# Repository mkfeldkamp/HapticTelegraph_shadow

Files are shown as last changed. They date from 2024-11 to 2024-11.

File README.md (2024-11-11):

# HapticTelegraph

The Haptic Telegraph is an open-source educational project to learn the basics of mechatronic sensing and control of motion, force, and impedance for one or more degrees or freedom along with basi teleoperation.  Inspired by the [HapKit](https://hapkit.stanford.edu/) open source Haptics learning project, the the haptic telegraph has two degrees of freedom (DOF) with the option to teleoperate over the internet and interconnect different haptic telegraphs to experiment with bilateral teleoperation.  

The platform uses a Teensy 4.0 microcontroller and breadboard to allow prototyping and easier modifications.  Sensing includes potentiometers, encoders, and load cells (HX711); actuators include hobby servos, N20 gearmotors, and direct-drive DC motors; an DRV8833 H-Bridge for driving up to two DC motors, and a simple way of attaching actuators in various configurations.  This includes side-by-side configurations or serlial linkages like a 2-link revolute joint robot with integrated torque sensing. 

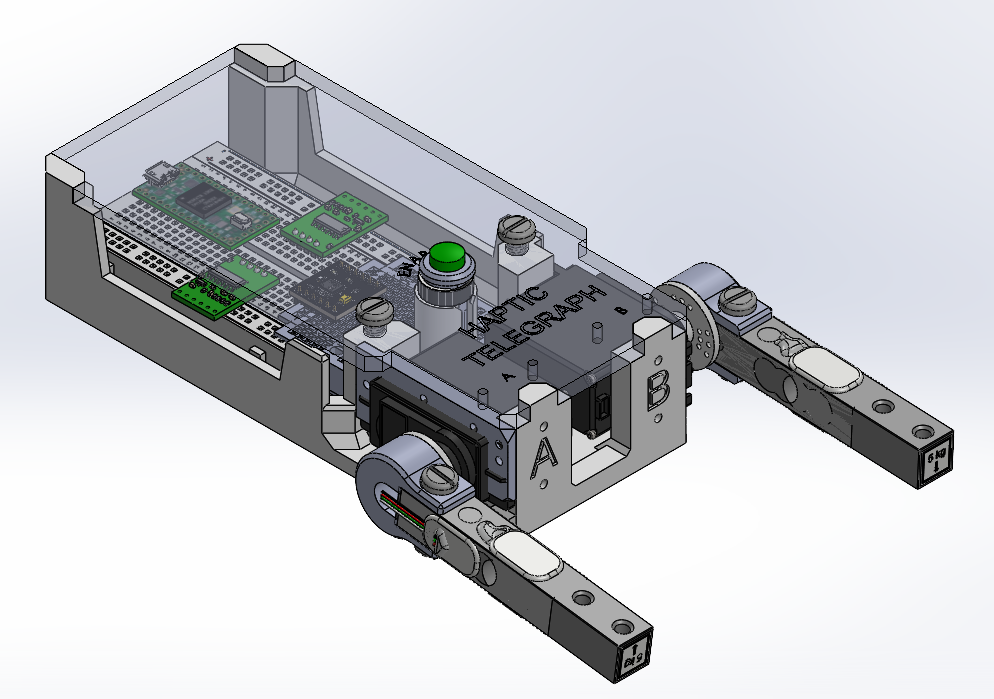
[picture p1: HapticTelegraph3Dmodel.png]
The Haptic Telegraph


## Building and Assembly 
All parts required for the different configurations of the telegrpaph are linked here.  The kit has hobby servo motors, N20 gear motor+encoders, direct drive DC motor for capstan, or DC motorized slide-potentiometer actuators.  The servo and N20 configurations are the default.  

[Haptic Telegraph Assembly Guide](https://docs.google.com/document/d/17Dt6qZLQLV2zLom0jG1yqs2Jcs7Xk3iRWMrtn3mGbbk/preview)

[BOM and Kit Inventory](https://docs.google.com/spreadsheets/d/1TIM3guZMqlwLRaXGF0uH3Ged3IqBKqTgrUTtAIh1ZG8/preview)

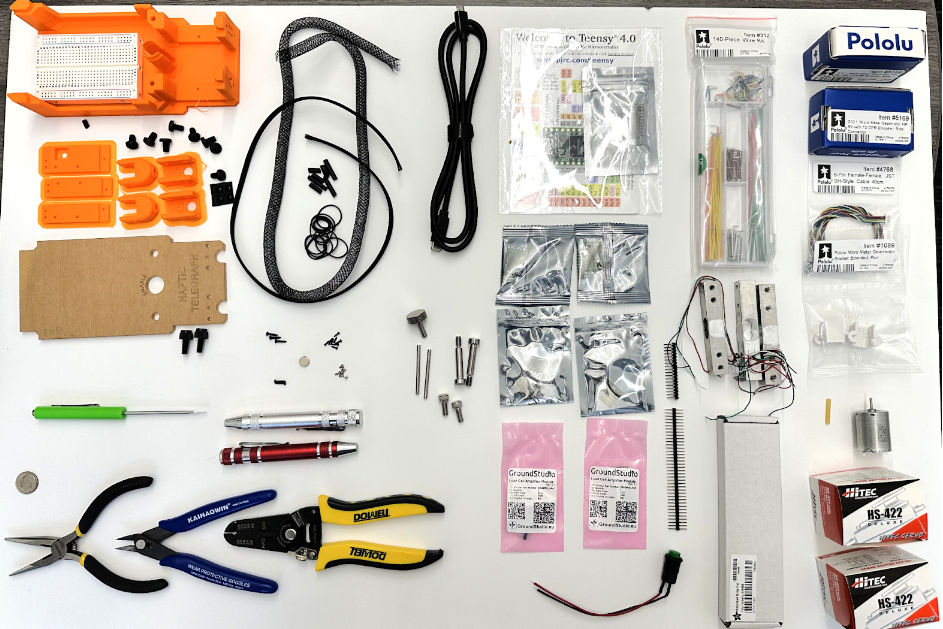
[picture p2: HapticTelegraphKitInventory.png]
Parts Kit Inventory


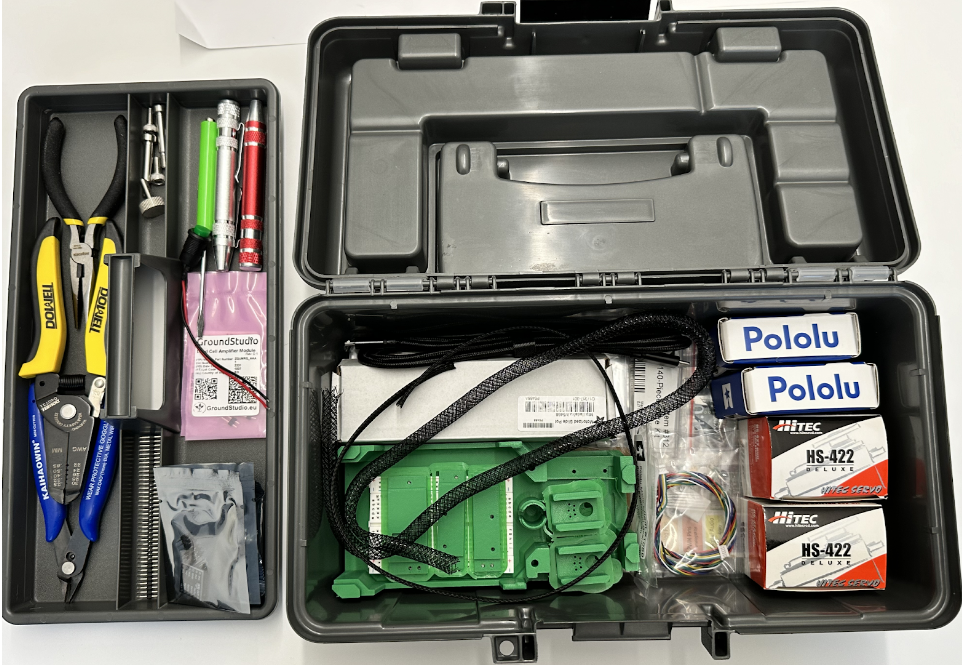
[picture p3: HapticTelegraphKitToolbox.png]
Kit Toolbox


## Software and Firmware
A brief introduction to the python scripts to teleoperate the kit and to run the firmware can be found here: <br>
[Haptic Telegraph Software Guide](https://docs.google.com/document/d/1zL3_G8BJS4lk9wN5zXE0Af6u3FeUNIUszWQ2UWdJn5c/preview)

## Resources
A great intro to haptics, teleoperation, and related terminology can be found here:
[Do It Yourself Haptics: Part I](https://ieeexplore.ieee.org/document/4437756)    
V. Hayward and K. E. Maclean, "Do it yourself haptics: part I," in IEEE Robotics & Automation Magazine, vol. 14, no. 4, pp. 88-104, Dec. 2007, doi: 10.1109/M-RA.2007.90792

A widely acclaimed, more thorough treatment from Prof. Allison Okamura is here:
https://web.stanford.edu/class/me327/

### Info
ME8284 Intermediate Robotics with Medical Applications Graduate Level Course <br>
University of Minnesota Mechanical Engineering, Fall 2024 <br>
Prof. Timothy M. Kowalewski, timk@umn.edu
Pin-Hao Cheng, cheng741@umn.edu

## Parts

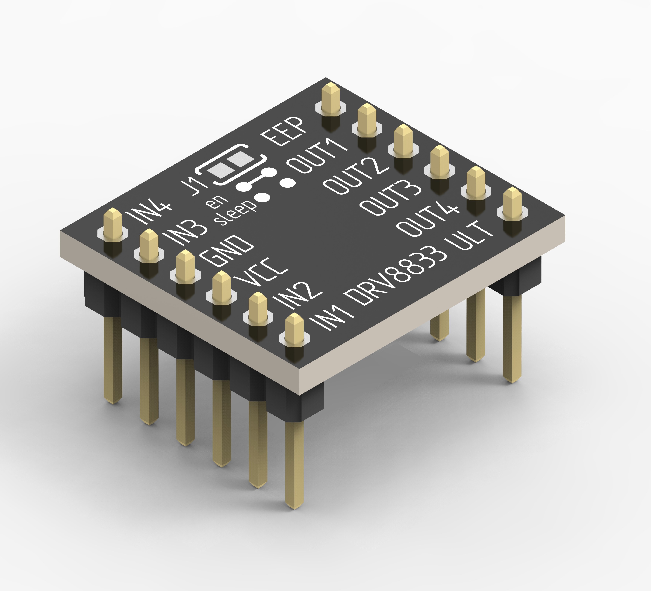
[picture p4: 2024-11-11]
mechanical/stockParts/etc/drv8833-doble-puente-h-dual-h-bridge-motor-driver-1.snapshot.3/Modulo DRV8833/Renders/Modulo_DRV8833_B.24.jpg

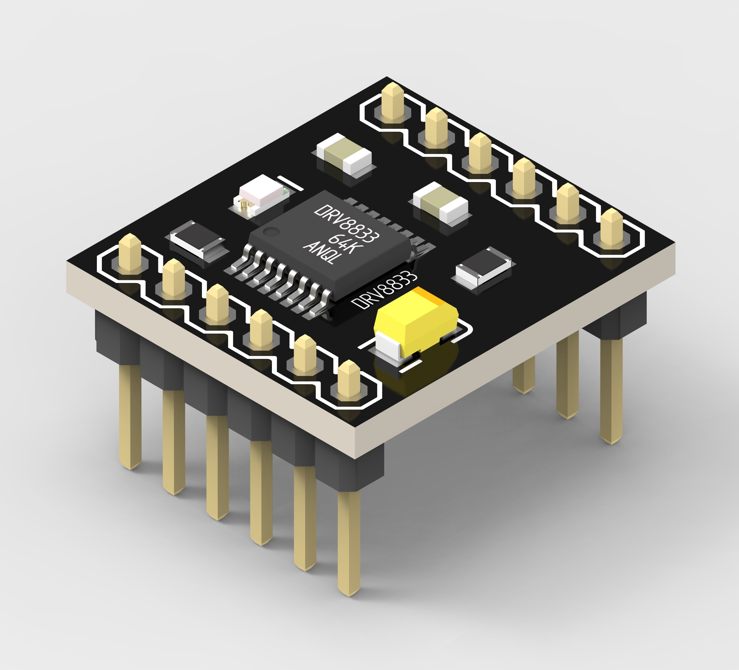
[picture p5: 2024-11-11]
mechanical/stockParts/etc/drv8833-doble-puente-h-dual-h-bridge-motor-driver-1.snapshot.3/Modulo DRV8833/Renders/Modulo_DRV8833_A.jpg

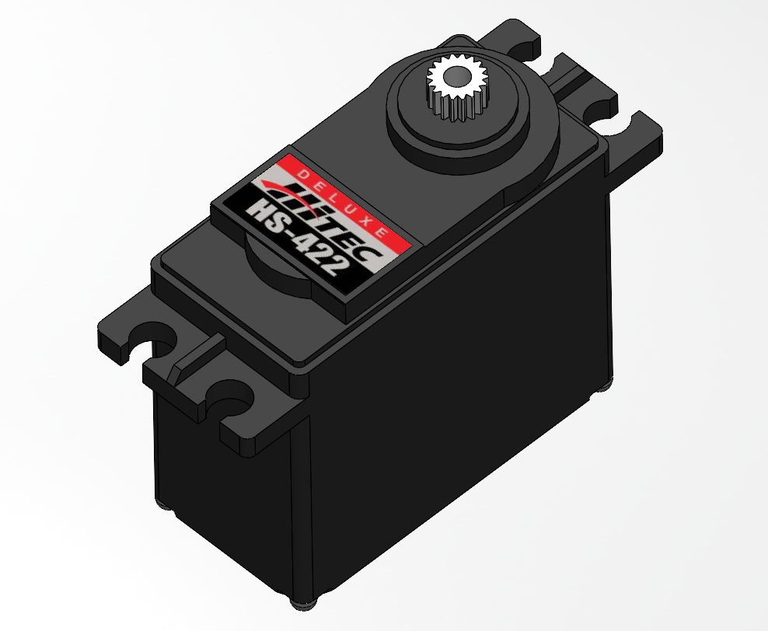
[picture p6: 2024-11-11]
mechanical/stockParts/etc/hitech-servo-hs-422-1.snapshot.10/Renders/Hitec-422 ServoMotor 1.png

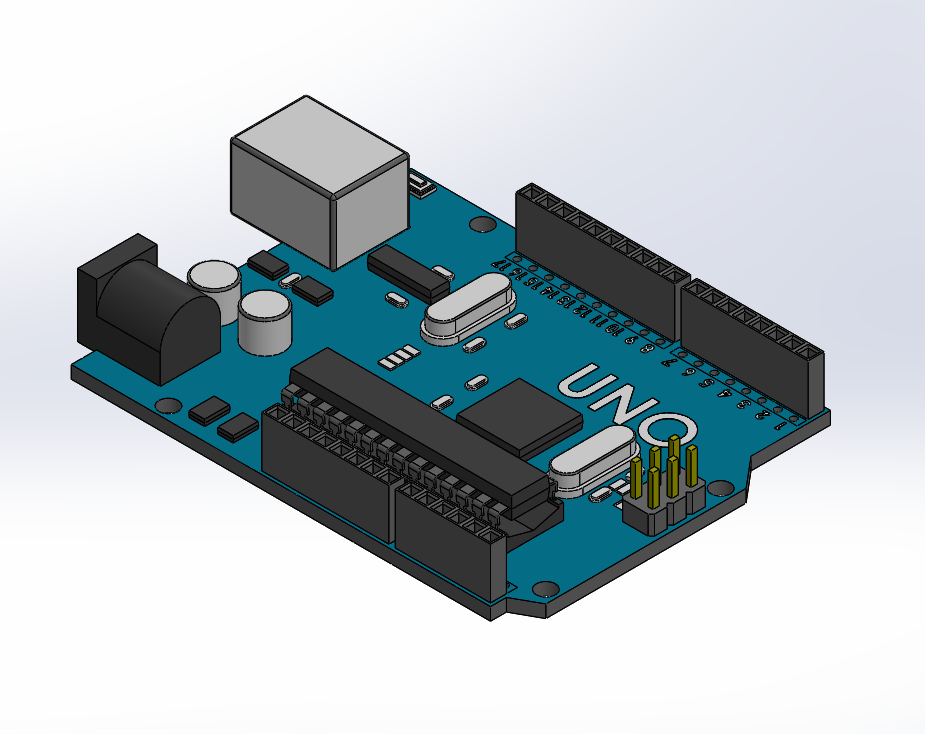
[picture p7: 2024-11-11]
mechanical/stockParts/etc/arduino-uno-62.snapshot.2/Arduino UNO.png

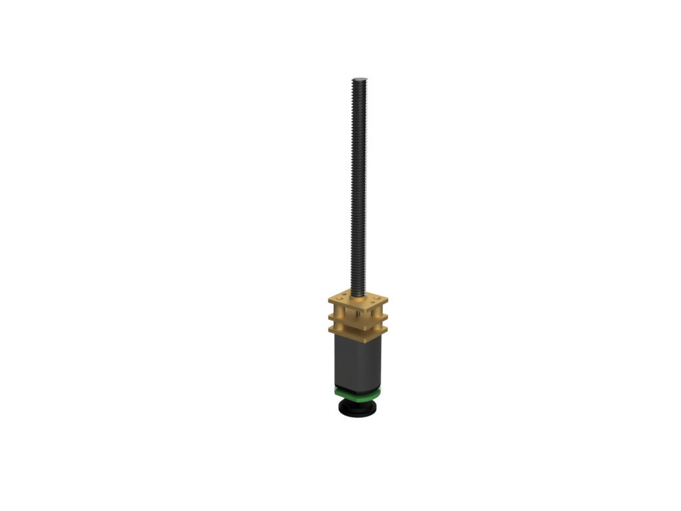
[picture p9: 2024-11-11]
mechanical/stockParts/etc/n20-gearbox-encoder-m4x55mm-1.snapshot.3/n20 encoder m4x55.png

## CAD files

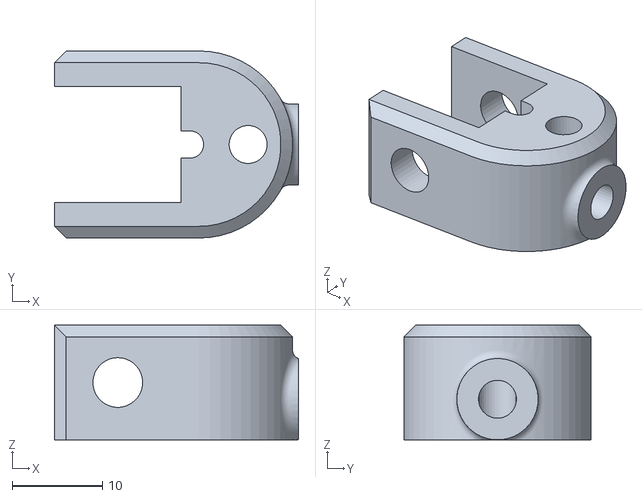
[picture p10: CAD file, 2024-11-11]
mechanical/3D printing and gCode/D Shaft Coupling N20.STL
27.0 x 20.7 x 12.7

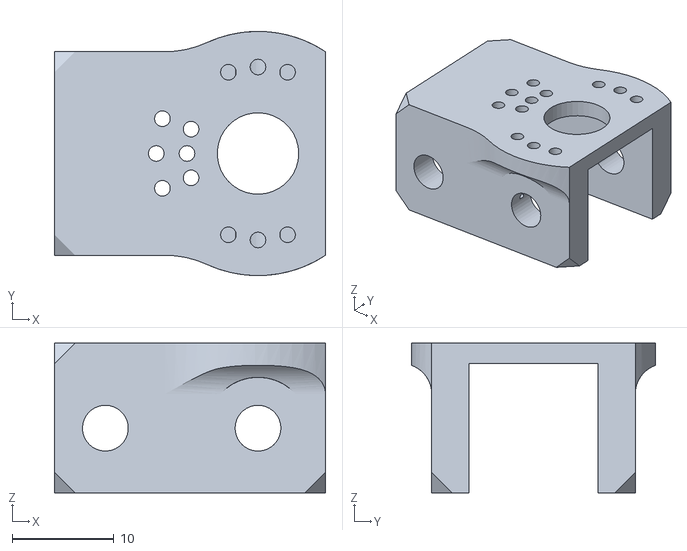
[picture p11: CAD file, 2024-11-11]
mechanical/3D printing and gCode/TOpRINT/1kg 80mm Load Cell Servo Horn Mount.STL
26.6 x 24.0 x 14.7

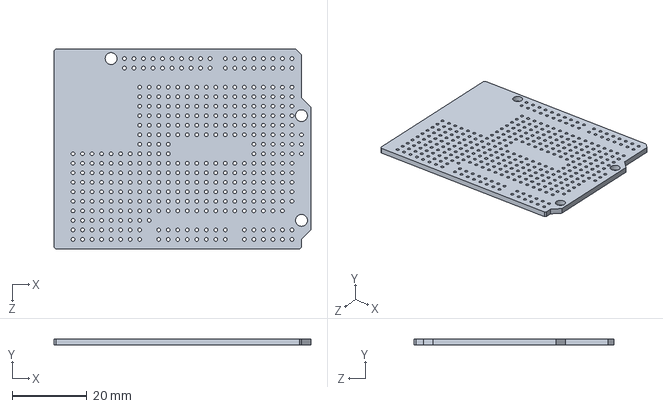
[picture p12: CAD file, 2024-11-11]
mechanical/stockParts/etc/arduino-proto-shield-r3.snapshot.3/Arduino proto shield R3.SLDPRT
68.6 x 1.70 x 53.3 mm

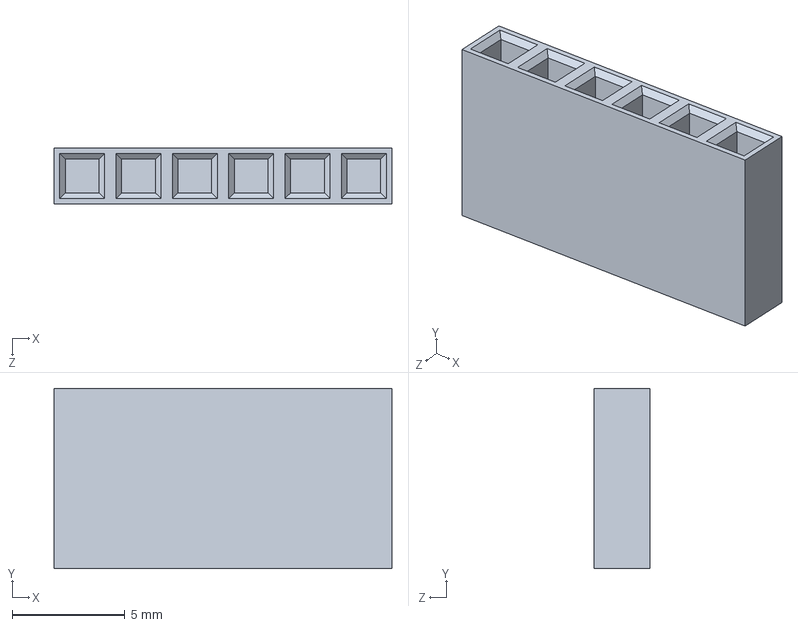
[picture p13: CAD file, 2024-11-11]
mechanical/stockParts/etc/arduino-uno-62.snapshot.2/Pins Socket 4.SLDPRT
15.0 x 8.00 x 2.50 mm

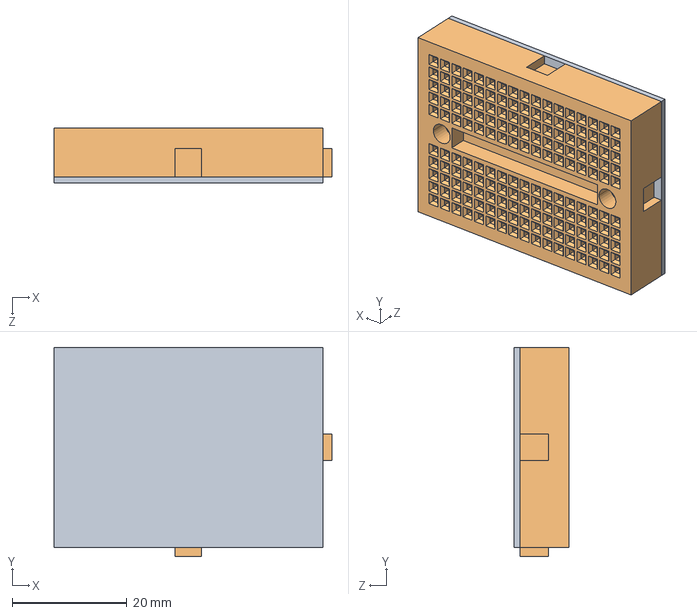
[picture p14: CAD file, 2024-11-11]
mechanical/stockParts/etc/breadboard-22.snapshot.4/BreadBord.STEP
48.4 x 36.4 x 9.50 mm

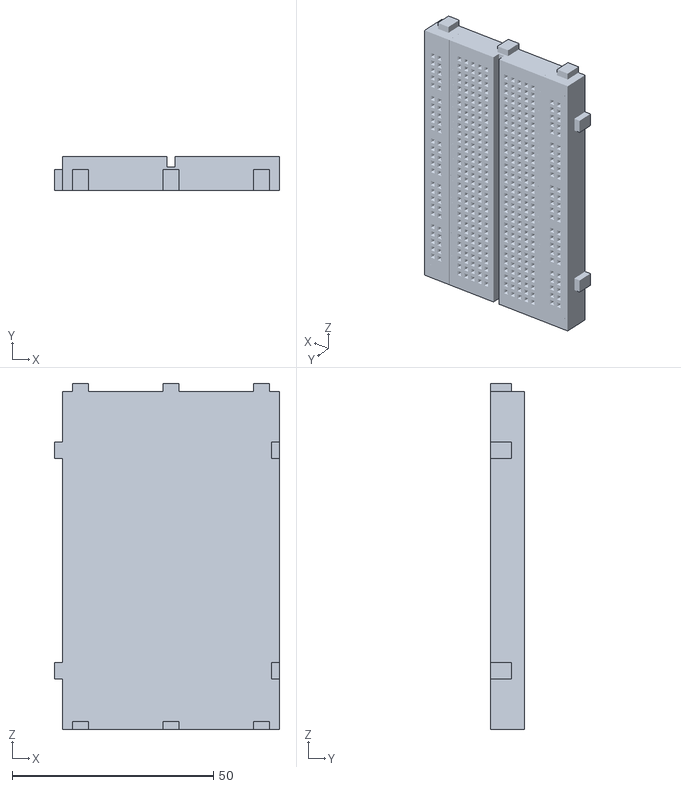
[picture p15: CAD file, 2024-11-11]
mechanical/stockParts/etc/breadboard-400-1.snapshot.5/Breadboard 400.stl
56.0 x 8.41 x 86.0

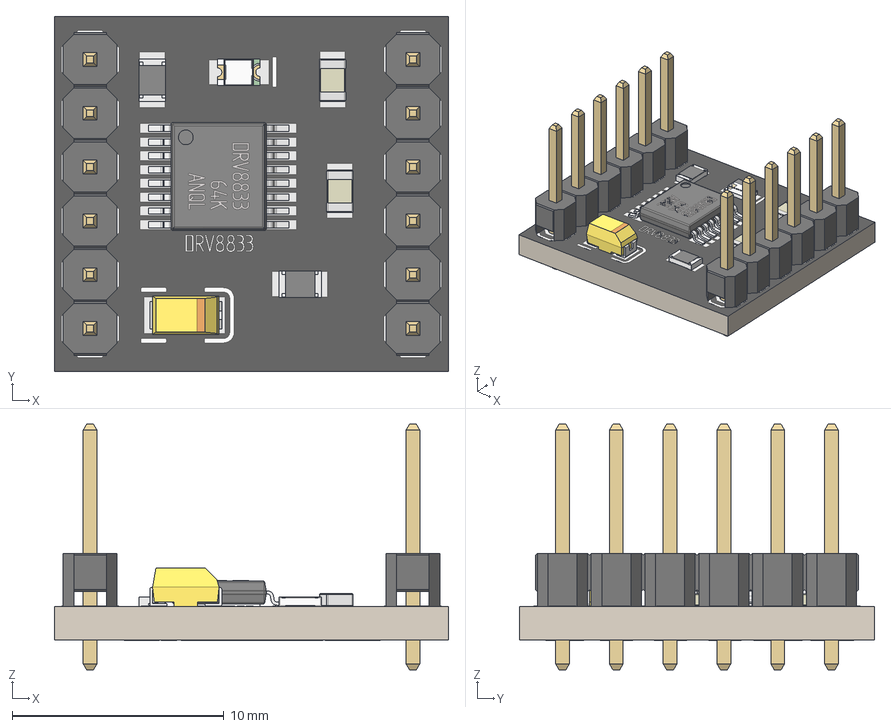
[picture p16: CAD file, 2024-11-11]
mechanical/stockParts/etc/drv8833-doble-puente-h-dual-h-bridge-motor-driver-1.snapshot.3/Modulo DRV8833/Modulo_DRV8833_B.stp
18.6 x 16.8 x 11.6 mm
placa
TSSOP_cuerpo_1.2h
TSSOP_pin_6.6 x 2
PIN_macho_1x6 x 2
T494A
C0805_060 x 2
R0805 x 2
housing
marking x 2
cover
base_2
base

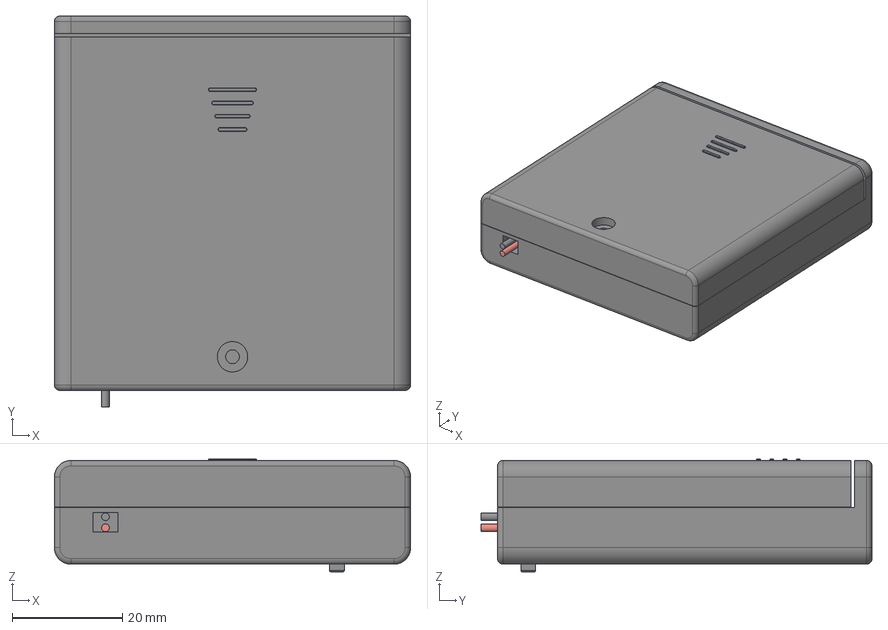
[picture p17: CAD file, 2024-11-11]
mechanical/stockParts/etc/enclosed-4-aa-battery-holder-1.snapshot.25/batteryHoder.step
64.5 x 70.8 x 20.4 mm

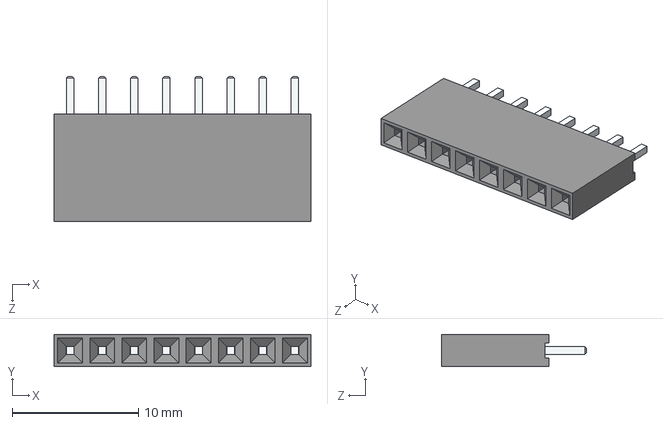
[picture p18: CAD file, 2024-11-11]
mechanical/stockParts/etc/female-header-2-54-1xn-1.snapshot.3/FemaleHeader.STEP
20.3 x 2.54 x 11.5 mm

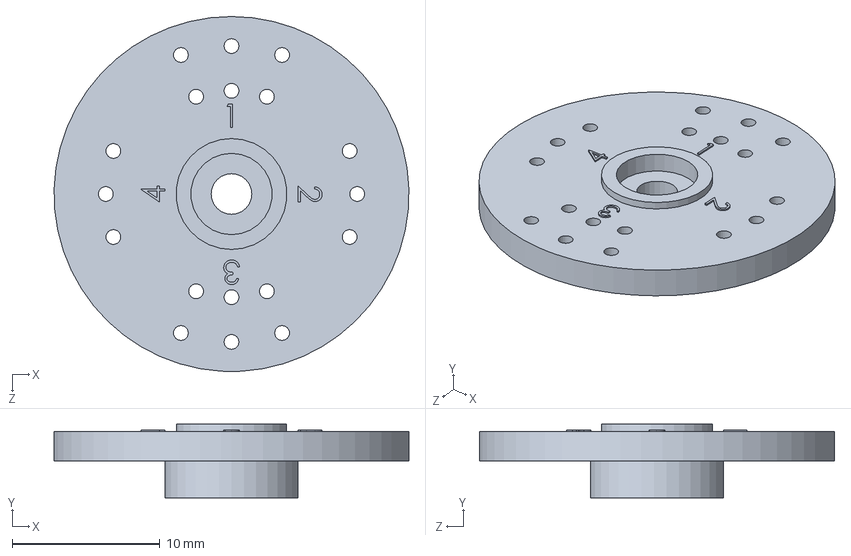
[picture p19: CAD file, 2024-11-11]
mechanical/stockParts/etc/hitec-hs-422-servo-horn-disc-1.snapshot.1/hs-422_horn_disc_sws(1).SLDPRT
24.0 x 5.00 x 24.0 mm

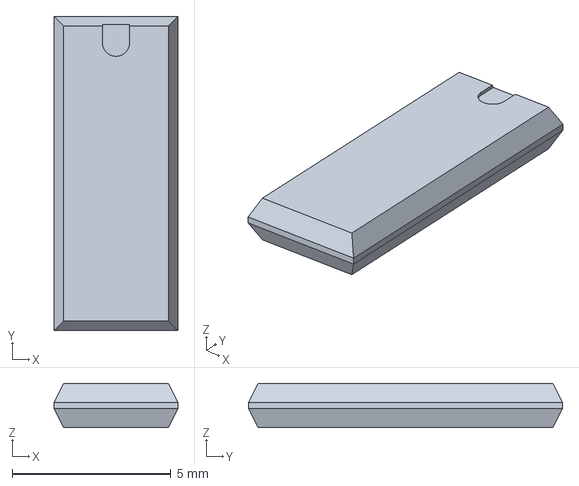
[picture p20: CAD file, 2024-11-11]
mechanical/stockParts/etc/hx711-strain-gauge-amplifier-module-with-round-pin-socket-headers-1.snapshot.1/HX711 (FreeCAD)/SOP-16L.FCStd
3.90 x 9.90 x 1.40 mm

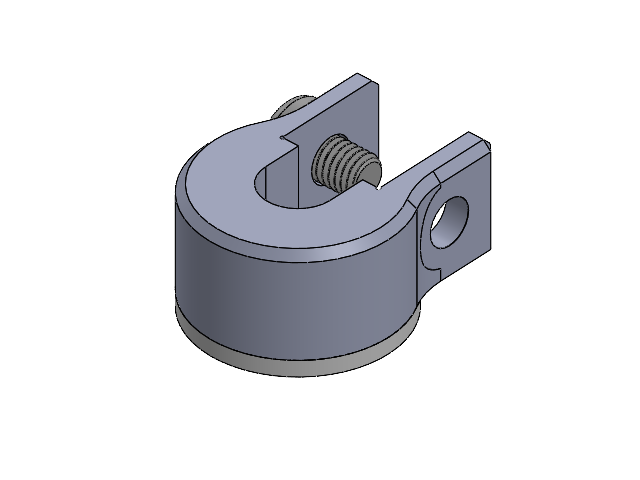
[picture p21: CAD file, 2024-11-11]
mechanical/ServoLoadCell.SLDASM
hs-422_horn_disc
LoadCellHornHub^ServoLoadCell
90451A318_Black Nylon Slotted Rounded Head Screws

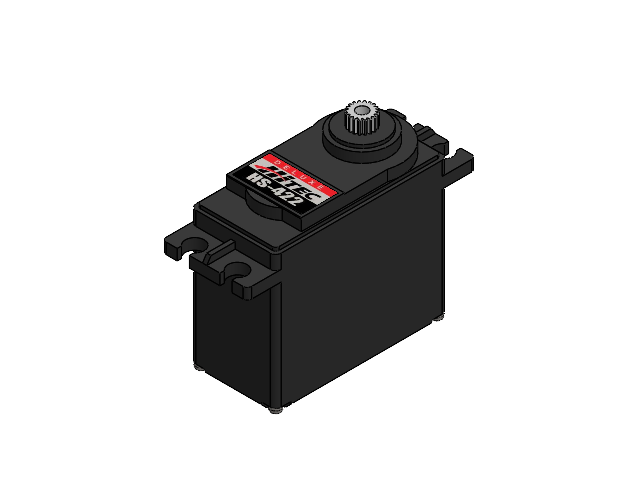
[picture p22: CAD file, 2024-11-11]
mechanical/stockParts/etc/hitech-servo-hs-422-1.snapshot.10/Assembly Hitec Servo.SLDASM
Servo Frame HGR
Servo Geared Tooth HGR
Hitec-422 Plate HGR
Servo Screw HGR x 4

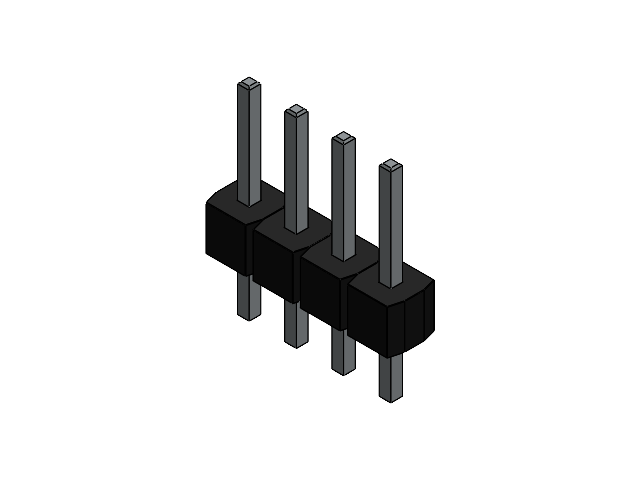
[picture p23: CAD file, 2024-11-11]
mechanical/stockParts/MaleHeader 4pin.SLDASM
Spacer x 4
Male Header Pin x 4

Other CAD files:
mechanical/1kgServoMount.SLDASM
mechanical/1kgServoMount2.SLDASM
mechanical/stockParts/etc/arduino-uno-62.snapshot.2/IC Assembly.SLDASM
mechanical/stockParts/TeensyBreadboard.SLDASM
mechanical/1kg 80mm Load Cell HOLE DRILLING JIG.SLDPRT
mechanical/1kg 80mm Load Cell Servo Horn Mount.SLDPRT
mechanical/3D printing and gCode/Base^HapticTelegraph vBeta.STL
mechanical/3D printing and gCode/Distal Joint Mount^N20 Load Cell.STL
mechanical/3D printing and gCode/Haptic Telergaph ALL PARTS.3mf
mechanical/3D printing and gCode/Haptic Telergaph JIGS.3mf
mechanical/3D printing and gCode/Haptic Telergaph some PARTS.3mf
mechanical/3D printing and gCode/LoadCellHornHub^ServoLoadCell.STL
mechanical/3D printing and gCode/TOpRINT/1kg 80mm Load Cell HOLE DRILLING JIG.STL
mechanical/3D printing and gCode/TOpRINT/Base^HapticTelegraph vBeta.STL
mechanical/3D printing and gCode/TOpRINT/D Shaft Coupling N20.STL
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

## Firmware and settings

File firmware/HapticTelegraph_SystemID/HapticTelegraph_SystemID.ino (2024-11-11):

// This reads encoder values using a hardware timer interrupt and ring buffer
// A timer interrupt (timer1 16-bit timer) is used
// dumps data to serial port.  Test signals can be sent to motors; 
// PWM command, timestamps, and all sensors are dumped to serial for plotting/analysis

#include <ADC.h>    // Analog to Digital Conversion library (avoids blocking time of native analogRead())
#include <HX711.h>  // https://github.com/bogde/HX711 bodge's library

//  ****  ENCODER SECTION    *****      //
#define ENC_TICKS_PER_REV 12.0f  //8192 CUI; N20 motors have 12 CPR HALL encoder      // encoder ticks per revolution
#include <Encoder.h>
// Change these two numbers to the pins connected to your encoder.
//   Best Performance: both pins have interrupt capability
//   Good Performance: only the first pin has interrupt capability
//   Low Performance:  neither pin has interrupt capability
//   Avoid using pins with LEDs attached
//Encoder myEnc(10, 11);                                              // must be 2,3 on arduino UNO, any digital pin on Teensy
// const float ticksToDegrees = 360.0 / (ENC_TICKS_PER_REV * 298.0f);    // 298:1 gear ratio
const float ticksToDegrees = 360.0 / (ENC_TICKS_PER_REV * 100.0f);    // 100:1 gear ratio


///////////////////////////////////////////////////////////////////////////////////////////////////
// GLOBAL VARIABLES  -- will be used by interrupts
volatile int motorPWMcmdA = 0;  // The actual low-level signed pwm command used by runMotorA
volatile int motorPWMcmdB = 0;  // e.g. motorPWMcmdA = desiredPWM + ditherPWN + deadBand ...
volatile int potA, potB;        // global variable for pot position reads (raw values)
volatile int encA, encB;        // raw values 
volatile int forceA, forceB;    // converted force values in grams-force.
///////////////////////////////////////////////////////////////////////////////////////////////////

///////////////////////////////////////////////////////////////////////////////////////////////////
// Constants (in TitleCase;  variables are in camelCase)
// pins 7 & 8 reserver for TimerOne https://www.pjrc.com/teensy/td_libs_TimerOne.html
const char LedPin = 13;           // 13 is LED on teensy; will use it to indicate motors are live
const char MotorEnablePin = 12;   // Reads sleep pin on HX711; driven by Enable Switch; HIGH --> ON
const char MotorA1pin     =  4;   // Motor command pins (feeds into input of DRV8833 H bridges)
const char MotorA2pin     =  5;   // swaping 1 and 2 will reverse direction of motor
const char MotorB1pin     = 18;   //
const char MotorB2pin     =  6;   // 
const char LoadCellA_SCKpin = 1;  // HX711 Load cell pins;  Check carefully; one writes, one reads
const char LoadCellA_DTpin  = 0;  //  DT: Data outpt from load cell (to teensy, which reads it)
const char LoadCellB_SCKpin = 3;  //  SCK: Clock input to load cell (from teensy, which writes it)
const char LoadCellB_DTpin  = 2;  //

// Load cell calibration values ...
const float LoadCellA_scale = 420.1;  // 5kg  TODO: you need to calibrate this yourself.
const float LoadCellB_scale = 420.0;  // 5kg  scale*RawLoadCell = grams
HX711 loadCellA;
HX711 loadCellB;
// Motor feedback; N20 gear motors have digital encoders, servo's have analog potentiometers
// make sure encoder pins are interruptable
const char EncApin_aw = 8;   // Motor A; enoder channel a, white wire
const char EncApin_by = 9;   // Motor A; enoder channel b, white wire
const char EncBpin_aw = 10;  // Motor B; enoder channel a, white wire
const char EncBpin_by = 11;  // Motor B; enoder channel b, white wire
// const float EncCountsToDeg = 360.0f / (12.0f * 100.0f);  // Encoder counts per revol. (CPR) x Gear Ratio;
const float EncCountsToDeg = 360.0f / (12.0f * 298.0f);  // Encoder counts per revol. (CPR) x Gear Ratio;
Encoder encoderA(EncApin_aw, EncApin_by);
Encoder encoderB(EncBpin_aw, EncBpin_by);

// Potentiometer position feedback (modified servo)   TODO: you find these three vals for each servo
const char PotApin    = A1;                             // Servo A potentiometer
const char PotBpin    = A0;                             // Servo B potentiometer
const int PotMinA     = 43;                             // end stop of servo
const int PotMaxA     = 976;                            // end stop of servo
const float RngDegA   = 195;                            // endstop-to-endstop travel in degrees (use protractor)
const float Pot2DegA  = RngDegA / (PotMaxA - PotMinA);  // degree per pot val
const int PotMinB     = 44;                             // end stop of servo
const int PotMaxB     = 976;                            // end stop of servo
const float RngDegB   = 195;                            // travel between end stops in degrees
const float Pot2DegB  = RngDegB / (PotMaxB - PotMinB);  // degree per pot val


// Each servo has unique pots; compute servo-specific degrees here
inline float getServoPosA() {
  potA = analogRead(PotApin);
  return ((float)potA - PotMinA) * Pot2DegA - 90.0;  // make origin 0 so +/-90deg travel
}
inline float getServoPosB() {
  potB = analogRead(PotBpin);
  return ((float)potB - PotMinB) * Pot2DegB - 90.0;
}


// Motor items; PWM resolution and frequency; see https://www.pjrc.com/teensy/td_pulse.html
const int PwmResolution = 12;
const int MaxPWM = pow(2, PwmResolution) - 1;  // e.g. 8bit resolution has 255 max
const int PwmFrequency = 00;                  // Hz
const int PwmDitherMax = MaxPWM*20/100.0f ;         // e.g. dither with 20% of MaxPWM

// runs a motor and handles negative values (reverses H bridge, applies PWN
// takes values  -MaxPWM <= u <= MaxPWM  where MaxPWM is max 100% pwm write of analogWrite()
inline void runMotorA(int u) {
  // for negative u, run H-bridge in reverse; otherwise just pass command through
  motorPWMcmdA = u;
  if (motorPWMcmdA < 0) {
    // if ( motorPWMcmdA < -MaxPWM) {
    //   Serial.println("% Warning: Clipping motor output to " + String(-MaxPWM));
    //   motorPWMcmdA = MaxPWM;
    // }
    analogWrite(MotorA1pin,  0            );
    analogWrite(MotorA2pin, -motorPWMcmdA );
  } else {
    // if ( motorPWMcmdA> MaxPWM) {
    //   Serial.println("% Warning: Clipping motor output to " + String(MaxPWM));
    //   motorPWMcmdA = MaxPWM;
    // }
    analogWrite(MotorA1pin,  motorPWMcmdA );
    analogWrite(MotorA2pin,  0            );
  } 
}

inline void runMotorB(int u) {  
  //motorPWMcmdB = u;
  // for negative u, run H-bridge in reverse; otherwise just pass command through
  if ( u < 0) {
    analogWrite(MotorB1pin,  0            );
    analogWrite(MotorB2pin, -u );
  } else {
    analogWrite(MotorB1pin,  u );
    analogWrite(MotorB2pin,  0            );
  }
}



// ****  HARDWARE TIMER SECTION  ****    //
// Use Timer1 (16-bit timer that does not mess with millis(), micros() or arduino scheduler which uses
// timer0 (8bit)
// https://www.pjrc.com/teensy/td_libs_TimerOne.html
#include <TimerOne.h>
#define LED_PIN 13
// Sample period of timer interupt service routine (ISR) in microseconds
//#define   TIMER_PERIOD 100000 // e.g. set a timer of length 100000 microseconds (or 0.1 sec - or 10Hz)
#define TIMER_PERIOD 1000  // e.g. 1000us = 1ms =>  1 KHz update rate.


// ****  SERVO SECTION       **** ////
#include <Servo.h>
#define SERVO_PIN 23
Servo myservo;  // unmodified servo 

// // ****** MOTOR PWM / H-Bridge Section   *** //
// #define MOT_A 18
// #define MOT_B 6
// volatile int u;  // motor command global variable.
// void motorCommand(int uPWM) {

//   if (u < 0) {
//     analogWrite(MOT_A, -uPWM);
//     analogWrite(MOT_B, 0);
//   } else {
//     analogWrite(MOT_A, 0);
//     analogWrite(MOT_B, uPWM);
//   }
//   return;
// }

//   ****  RING BUFFER SECTION ****     ///
// A ring buffer.  Allows you to write data VERY quickly inside an interrupt.  Can read it later in chunks
// to write to ring buffer, write myDataSample to: iWrite = (currentIndex+1) % BUF_LENGTH location along BUF_LENGTH;
//                          THEN, WHEN DONE WRITING: set lastWritten = iWrite
// to read from ring bufffer, read myDataSample from: iRead = (currentIndex+1) % BUF_LENGTH location;
//                          THEN, WHEN DONE READING: set lastread = iRead
#define BUF_LENGTH 10000  // number of entries in ring buffer before overflow (positive integer, needs to be long enough to not overrun)
#define BUF_DIMENSION 1   // dimmension of buffer  (e.g. number of encoders and therefore dataSamples per time sample)
struct myDataSample {
  unsigned long int t;    // time of sample (micro sec)
  int   motorPWMcmdA;     // actual motor command (no dither or compensation) at this time sample
  int   motorPWMcmdB;     // ...
  float forceA;           // load cell force (with unit conversion) 
  float forceB;           // load cell force (with unit conversion)     
  int   encA;             // encoder reading at this time sample
  int   encB;             // ...
  int   potA, potB;       // potentiometers
  bool  bufferOverflow;   // 0 - all OK;  true - buffer overflowed and data corrupted.
};

// Instantiate the ringBuffer itself.
myDataSample ringBuffer[BUF_LENGTH][BUF_DIMENSION];
bool ringBufferOverflow;
volatile int lastWritten;  // using signed ints so that ( lastRead - 1 ) will behave nicely near zero, makes modulo arithmetic more intuitive.
volatile int lastRead;
volatile int iWrite, iRead;  // index values for bookeeping, a separate i for writing and reading.


/// --------------------------
/// Custom ISR Timer Routine  (ISR: Interrupt Service Routine, the function that gets called each time TIMER_PERIOD expires.
/// --------------------------
volatile unsigned long int tg;  // global time [micros]
volatile bool ditherToggle = 1; 
void inline timerIsr() {

  // Toggle LED
  //digitalWrite( LED_PIN, digitalRead( LED_PIN ) ^ 1 );         // can attach an o-scope to measure jitter on this pin directly

  // read sensors to global vars and get time
  volatile static unsigned long int t0 = micros();  // static vars only get initialized the first time function is called, persiste thereafter
  tg = micros() - t0;
  encA = encoderA.read();       encB = encoderB.read();       // should be very fast
  potA = analogRead( PotApin ); potB = analogRead( PotBpin ); // TO DO: use ADC library to make this fast. 
  // forceA =  loadCellA.get_units();  !! Cannot do this in ISR, long duration, blocking call. 


  // Get most recent data, write it to ring buffer.
  // to write to ring buffer, write myDataSample to: iWrite = (currentIndex+1) % BUF_LENGTH location along BUF_LENGTH;
  //                          THEN, WHEN DONE WRITING: set lastWritten = iWrite
  iWrite = (BUF_LENGTH + lastWritten + 1) % BUF_LENGTH;  // shift index to write to next entry

  if (iWrite == lastRead)       // This is bad; working code needs to ensure it never happens,
    ringBufferOverflow = true;  // if it does, data is overwritten; increase buffer length or reading frequency to avoid

  ringBuffer[iWrite][0].t = tg;                               // current time in microsec
  ringBuffer[iWrite][0].motorPWMcmdA = motorPWMcmdA;          // current motor commands (plant input u, no dither or open loop comp.)
  ringBuffer[iWrite][0].motorPWMcmdB = motorPWMcmdB;          // current motor commands (plant input u, no dither ...)
  ringBuffer[iWrite][0].forceA =  forceA;                     // get global forceA, won't update as fast and timestamp will stray
  ringBuffer[iWrite][0].forceB =  forceB;                     // get global forceA, won't update as fast and timestamp will stray
  ringBuffer[iWrite][0].encA = encoderA.read();               // current encoder position
  ringBuffer[iWrite][0].encB = encoderB.read();               // current encoder position
  ringBuffer[iWrite][0].potA = potA;                          // current pot val 
  ringBuffer[iWrite][0].potB = potB;                          // current pot val 
  ringBuffer[iWrite][0].bufferOverflow = ringBufferOverflow;  // tag if/when the buffer overflows
  lastWritten = iWrite;                                       // officially done writing the "next entry"

  // dither
  if ( ditherToggle )
    motorPWMcmdB += PwmDitherMax;
  else 
    motorPWMcmdB -= PwmDitherMax; 
  runMotorB( motorPWMcmdB );
  ditherToggle = !ditherToggle;   
}





/////////////////////////////////////////////////////////////////////////
//  **** SETUP -- only runs once; Set up buffer and timer here   ****  //
/////////////////////////////////////////////////////////////////////////

#define BANNER "% t[ms]  command[pwmA]  encPosA[ticks]  potA[raw]  command[pwmB]  encPosB[ticks]  potB[raw]   bufferOverflow \t iRead iToRead i "
unsigned long int enc, enc_1, enc_2;  // the current, previous, and previous-previous encoder readings
unsigned int j = 0, increasingDelay;
long oldPosition = -999;

float dT, t;

void setup() {

  // put your setup code here, to run once:
  pinMode(LedPin, OUTPUT);
  pinMode(MotorEnablePin, INPUT);
  pinMode(MotorA1pin, OUTPUT);
  pinMode(MotorA2pin, OUTPUT);    
  pinMode(MotorB1pin, OUTPUT);  
  pinMode(MotorB2pin, OUTPUT);
  analogWriteFrequency(MotorA1pin, PwmFrequency);
  analogWriteFrequency(MotorA2pin, PwmFrequency);
  analogWriteFrequency(MotorB1pin, PwmFrequency);
  analogWriteFrequency(MotorA2pin, PwmFrequency);

  // turn motors off, etc.
  digitalWrite(MotorA1pin, LOW);
  digitalWrite(MotorA2pin, LOW);
  digitalWrite(MotorB1pin, LOW);
  digitalWrite(MotorB2pin, LOW);
  digitalWrite(LedPin, digitalRead(MotorEnablePin));  // LED on means motors enabled
  analogWriteResolution(PwmResolution);            // analogWrite value 0 to 4095, or 4096 for high

  // load cell setup ...
  loadCellA.begin(LoadCellA_DTpin, LoadCellA_SCKpin);
  loadCellB.begin(LoadCellB_DTpin, LoadCellB_SCKpin);
  loadCellA.set_scale(LoadCellA_scale);  // TODO you need to calibrate this yourself.
  loadCellB.set_scale(LoadCellB_scale);  // TODO you need to calibrate this yourself.

  // reset the scale to zero = 0  (assume startup load is desired unloaded 0 value)
  loadCellA.tare();
  loadCellB.tare();

  // set encoder value at current position; fyi encoder resets each power cycle
  encoderA.write(0);
  encoderB.write(0);

  // run serial at 115200 or greater; will need to interact over serial with decent latency
  Serial.begin(115200);
  Serial.println("Haptic Telegraph is running...");
  myservo.attach(22);

  while (!Serial /*&& (millis() < 5000)*/) {}  // wait up to 5 seconds for Terminal
  Serial.begin(115200);
  Serial.println(BANNER);
  Serial.print("% PWM Freq: "); Serial.print(PwmFrequency) ;
  Serial.print(" TimerPeriod[us]: ") ;Serial.println(TIMER_PERIOD);
  Serial.flush();

  // while (!Serial.available()) { /* do nothing until a serial event is received like a key press */
  // }
  // Serial.readString(); // consume whatever line is on serial so loop will start with empty input buffer

  // Initialize Ring Buffer indexes so that next write and read will occur at 0 (both must be equal)
  lastRead = BUF_LENGTH - 1;
  lastWritten = BUF_LENGTH - 1;

  // Set the timer and attach it.  Once that happens buffer will start getting filled with entries each TIMER_PERIOD
  // That means you must periodically read (and therefore empty) the buffer fast enough so it does not overflow.
  Timer1.initialize(TIMER_PERIOD);   //
  Timer1.attachInterrupt(timerIsr);  // attach the service routine here
}



/////////////////////////////////////////////////////////////////////////////////////////////////////////////////////
//  the LOOP()
//     * must empty the buffer fast enough to prevent overruns.
//     * empties the buffuer to serial, computing differences and derivatives as it does so
//     * To test when bufferoverrun occurs, artificially increases a delay() each loop.
//
const float F0 = 2 * PI * 0.2;     // Initial freq. in rad/s
const float F1 = 2 * PI * 2;       // final freq. in rad/s
const float T = 20 * 1;            // time in ms to run a test signal like chirp
const float C = log(F1 / F0) / T;  // compute this constant once for faster processing in chirpExp
// chirp =  sin( t .*  F0 .* exp( t.*C ) /1000 );


int squareWave(int uL, int uH, int TL, int TH) {
  static unsigned char state = 0;  // holds state of state machine
  int out = 0;
  if (state == 0) {
    out = uL;
  } else if (state == 1) {
    out = uH;
  } else {
    state = 0;
  }

  return out;
}

void loop() {

  // first take force readings.  This will be slow and block until done.  Then do timestamps, etc. 
  // onlt take both readings if you have to.  One or zero if your task does not need force(s)
  // forceA = loadCellA.get_units(); 
  forceB = loadCellB.get_units(); 
  
  static unsigned long int n = 0 /* num periods */, repsSoFar = 0; /* how many square wave period epochs of n have happened so far */
  //t = (micros() - t0) / 1000000.0;  // t in sec (now)
  //u = MaxPWM/2.5 * (1 - cos(t*F0) ) / 2.0;  // constant sine wave
  //u = 90 * ( 1 - cos(t*F0 * exp( t*C )) );  // chirp wave from F0 to F1
  //if( t > 5) return;
  //u =  int(t*100.0) % 300;//int(t) % PWM_MAX ;

  // SQUARE WAVE
  static int u, uL = MaxPWM * 100 / 100, uH = MaxPWM * 0 / 100;  // amplitude high and low of square wave
  static float T0 = 1000, T1 = 1000 + T0;                        //duration [ms]:  (end of) low and high  part of square wave
  static int state = 0;
  static unsigned long int tt0 = millis(), tt;  // a second timer just for wave generator
  tt = millis() - tt0;
  // Serial.print(" tt, T0 , tt>T0: ");
  // Serial.print(tt); Serial.print(" ");
  // Serial.print(T0); Serial.print(" ");
  // Serial.print(tt > T0); Serial.println(" ");
  if (state == 0) {
    u = uL;
    if (tt > T0) {
      state = 1;
    }
  } else if (state == 1) {
    u = uH;
    if (tt > T1) {
      state = 0;
      u = uL;          // smooth transition to avoid time back-jumps in plotting
      tt0 = millis();  // reset time for next run
      n++;             //Serial.print(" Done with State 1 ");
    }
  }  //else { state = 0; }

  u = 30; // can write a constant value here.
  motorPWMcmdB = 0;
  runMotorA(u);
  //runMotorB(  );

  //myservo.write( u );
  //myservo.writeMicroseconds(  1500 + u );

  // ////////////////////////////////////////////////////////////////////////////////////////////////////
  // RING BUFFER CODE
  // Empty entire ringBuffer to Serial...
  // to read from ring bufffer, read myDataSample from: iRead = (currentIndex + 1) % BUF_LENGTH location;
  //                          THEN, WHEN DONE READING: set lastread = iRead
  // First, if the buffer has overflowed, freak out.  This should never happen
  if (ringBufferOverflow)
    Serial.println("ERROR:  Ring buffer overflowed!  ... cannot trust data integrity going forward, increase buffer length?");

  // How many unread entries are there to read right now?
  int numToRead = (BUF_LENGTH + lastWritten - lastRead) % BUF_LENGTH;

  // read and process each entry one at a time.  incrementing lastRead as you do so...
  for (int i = 0; i < numToRead; i++) {

    iRead = (BUF_LENGTH + lastRead + 1) % BUF_LENGTH;  // start reading next entry (one entry at a time per each i iteration)

    // do math and unit conversion or other calculuations like floating point HERE, not in any Interrupt Service Routine (ISR) code.
    // ringBuffer[iRead][0].posEncA = ringBuffer[iRead][0].enc * ticksToDegrees;
    // ringBuffer[iRead][0].posEncB = ringBuffer[iRead][0].enc * ticksToDegrees;
    // ringBuffer[iRead][0].posPotA = getServoPosA();
    // ringBuffer[iRead][0].posPotB = getServoPosB();
    //ringBuffer[iRead][0].vel = ringBuffer[iRead][0].pos - ringBuffer[(BUF_LENGTH + iRead - 1) % BUF_LENGTH][0].pos;
    //ringBuffer[iRead][0].acc = ringBuffer[iRead][0].vel - ringBuffer[(BUF_LENGTH + iRead - 1) % BUF_LENGTH][0].vel;

    // compute deltaT, how much time elapsed since the previous sample, in seconds.  Should be same as SAMPLE_PERIOD/1000.0
    //dT = ringBuffer[(BUF_LENGTH + iRead ) % BUF_LENGTH][0].t     -     ringBuffer[(BUF_LENGTH + iRead - 1) % BUF_LENGTH][0].t ; // diff in us
    //dT = dT / 1000000.0 ;  // diff in sec.
    // scale .pos differences by this amount to return .vel and .acc in /sec.
    //ringBuffer[iRead][0].vel = ringBuffer[iRead][0].vel / dT ;
    //ringBuffer[iRead][0].acc = ringBuffer[iRead][0].acc / dT ;

    // output to serial as ASCII
    Serial.print(ringBuffer[iRead][0].t / 1000.0, 2);
    Serial.print("    ");   
    // Motor A ... 
    Serial.print(ringBuffer[iRead][0].motorPWMcmdA);
    Serial.print("  ");
    Serial.print(ringBuffer[iRead][0].potA);
    Serial.print("  ");
    Serial.print(ringBuffer[iRead][0].encA);
    Serial.print("    ");    
    Serial.print(ringBuffer[iRead][0].forceA);
    Serial.print("    ");    
    // Motor B ... 
    Serial.print(ringBuffer[iRead][0].motorPWMcmdB);
    Serial.print("  ");
    Serial.print(ringBuffer[iRead][0].potB);
    Serial.print("  ");
    Serial.print(ringBuffer[iRead][0].encB);
    Serial.print(" ");
    Serial.print(ringBuffer[iRead][0].forceB);
    
    // Serial.print(ringBuffer[iRead][0].pos, 2);
    //Serial.print( " " );
    //Serial.print( ringBuffer[iRead][0].vel , 2);
    //Serial.print( " " );
    //Serial.print( ringBuffer[iRead][0].acc , 2);
    //Serial.print( " \t % dT =  " ); Serial.print( dT  );
    Serial.print(" ");
    //Serial.print( iRead );
    Serial.print(" ");
    Serial.print(tt);
    Serial.println("");

    lastRead = iRead;  // officially done reading the iRead entry
    delayMicroseconds(1);
  }
  //Serial.flush();

  if (n > 0) {
    n = 0;
    u = 0;
    runMotorA(u);
    runMotorB(u);
    repsSoFar++;
    uL = uL * 90 / 100, uH = uH * 90 / 100;  // amplitude high and low of square wave; lower for next round by xx percent
    if (repsSoFar >= 35) {
      Serial.flush();
      while (!Serial.available()) { /* do nothing until a serial event is received like a key press */
      }
      Serial.readString();
      tt0 = millis();
    }
  }
}

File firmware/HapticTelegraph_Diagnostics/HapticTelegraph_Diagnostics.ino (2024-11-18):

/*
  Starter code for Haptic Telegraph.  Use for diagnostics and initial build. 
  Comment out uneeded sections in loop(): e.g., no pots, H bridge, or encoders?
  comment that stuff out to only display what you like.  Will run either way.
  Prof. Tim Kowalewski 2024
  Copyleft, public domain. 
*/

// #define ENCODER_USE_INTERRUPTS
#include <Encoder.h>        // Teensy encoder library Examples-->Teensy-->Encoder
#include "Adafruit_HX711.h" // Library Manager-->serach HX711 Adafruit --> intall
#include <Servo.h>    // Default Arduino servo library, only needed for UNMODIFIED servos
// note: Servo.h defines refresh rate of the pulse driving the servo position.  It's only 50Hz by default
// to speed it up change #define REFRESH_INTERVAL    20000     // minumim time to refresh servos in microseconds
// to something like 10000 (100Hz instead of 50Hz)  or whatever max your servo can take.
// analog servos are around 50Hz or a bit more; digital servos can often go up to 100's of Hz.

#include "HapticTelegraphPinsEtc.h"    // a literal copy-and-paste by the pre-processor (# commands)
                                       // tweak your pins, calibration vals, etc. in this .h file.
unsigned long int printPeriod = 50;    // printing update rate in ms, use ~50 for Serial Plotter
                                       
bool bTeleoperatingOverSerial = false; // false: dumps *all* diagnostic sensor/command vals to serial ***
                                       // true: suppresses diagnostic dump, sends /only* actuator A commands to
                                       //   serial (for processing in python or teleoperation over internet)
                                       //   and receives B commands from serial which drive local actuator B

// if bTeleoperationOverSerial==true, sends cmdA over serial to drive (command) distant actuatorB, 
// receives cmdB to drive local actuatorB; use python script to handle serial comm and UDP/IP traffic
float handleSerialTeleoperation(float cmdA, float cmdB);  // definition at bottom

///////////////////////////////////////////////////////////////////////////////////////////////////////
//   SETUP  Code in this function only runs once; initialize stuff, default values
///////////////////////////////////////////////////////////////////////////////////////////////////////
void setup() {

  // put your setup code here, to run once:
  // pinMode(MotorEnablePin, INPUT); //not used by default, 3.3 vs 5V tolerant ***
  pinMode(LedPin, OUTPUT);      digitalWrite(LedPin, HIGH);  // LED on means power is on  
  pinMode(MotorA1pin, OUTPUT);  pinMode(MotorA2pin, OUTPUT);
  pinMode(MotorB1pin, OUTPUT);  pinMode(MotorB2pin, OUTPUT);
  analogWriteFrequency(MotorA1pin, PwmFrequency); analogWriteFrequency(MotorA2pin, PwmFrequency);
  analogWriteFrequency(MotorB1pin, PwmFrequency); analogWriteFrequency(MotorA2pin, PwmFrequency);
  analogWriteResolution(PwmResolution);  // analogWrite value 0 to 4095, or 4096 for high

  // turn motors off, etc.
  digitalWrite(MotorA1pin, LOW);
  digitalWrite(MotorA2pin, LOW);
  digitalWrite(MotorB1pin, LOW);
  digitalWrite(MotorB2pin, LOW);

  // Adafruit Load cell setup ...
  loadCellAdaA.begin();
  loadCellAdaB.begin();
  // read and toss 3 values each to tare each load cell (select origin, 0 grams)
  Serial.println("Tare-ing load cell ...");
  for (uint8_t t = 0; t < 3; t++) {
    loadCellA_offset = loadCellAdaA.readChannelRaw(CHAN_A_GAIN_128);
    loadCellB_offset = loadCellAdaB.readChannelRaw(CHAN_A_GAIN_128);
  }

  // set encoder value at current position; fyi encoder resets home each power cycle,
  // cycling the enable button (h bridge power) does not reset encoder "home" position
  encoderA.write(0);
  encoderB.write(0);

  // if (unmodified) servos are used, initialize them here ...
  servoA.attach(ServoDrivePinA);  servoA.write(ServoInitialPosA);
  servoB.attach(ServoDrivePinB);  servoB.write(ServoInitialPosB);
  // move servos to confirm operation and sign (motion direction should be both up)
  delay(250);
  servoA.write(ServoInitialPosA - 10); servoB.write(ServoInitialPosB + 10);
  delay(250);
  servoA.write(ServoInitialPosA); servoB.write(ServoInitialPosB);
  
  // run serial at 115200 or greater; will need to interact over serial with decent latency
  Serial.begin(115200);
  Serial.println("Haptic Telegraph is running...");
}



///////////////////////////////////////////////////////////////////////////////////////////////////////
//   LOOP   This function will repeat until power down;  Put your main code here
///////////////////////////////////////////////////////////////////////////////////////////////////////
int cmdPWM = 0, delta = 1;
unsigned long t0, tPrint = 0;  // timestamps
float forceA, forceB, posA, posB;
float cmdA, cmdB, errA = 0, errB = 0;
void loop() {

  t0 = millis();

  // Read forces; for blocking call, will take 1/80Hz (~13ms)each; for nonblocking, returns immediately 
  // // BLOCKING:
  forceA = getLoadA();
  forceB = getLoadB();
  // NON BLOCKING: (useful if you can read position and write to H-bridge between loadcell reads)
  // if (!loadCellAdaA.isBusy())  forceA = getLoadA();
  // if (!loadCellAdaB.isBusy())  forceB = getLoadB();


  // posA = getModServoPosA();        // reads pot and returns degree pos from MODIFIED servo.
  // posB = getModServoPosB();
  // For unmodified servo. servoA.read() will just return whatever you sent via .write(), so not the
  // true position of the servo. But when needed you can still use:
  posA = servoA.read();  // UNMODIFIED SERVO, does not read true position, just written val
  posB = servoB.read();  // UNMODIFIED SERVO

  // read position via encoder (if installed, e.g. N20)
  posA = encoderA.read();
  posB = encoderB.read();

  ////////////////////////////////////////////////////////////////////
  // Print all values for serial plotter:
  // after printPeriod ms since the last print, go ahead and print...
  if ( millis() - tPrint >= printPeriod   &&   !bTeleoperatingOverSerial ) {
    Serial.print(" ForceA:");    Serial.print(forceA);    
    Serial.print(" ForceB:");    Serial.print(forceB);
    
    // Modified or unmodified servo pos.
    Serial.print("   ServoPosA:"); Serial.print(posA);
    Serial.print(  " ServoPosB:"); Serial.print(posB);
    
    // // N20 encoder position in deg, if encoders are unconnected, will just read 0.
    // Serial.print("  EncA:");  Serial.print(encoderA.read() * EncCountsToDeg);    
    // Serial.print(" EncB:" );  Serial.print(encoderB.read() * EncCountsToDeg);
    
    // // H-Bridge DC motor command
    // Serial.print("  cmdPWM:");  Serial.print(cmdPWM);
    // Serial.print(" MaxPWM:"+String(MaxPWM)); Serial.print(", ");

    // final commands to be sent to actuator A and B (inputs to plant)
    Serial.print("   cmdA:"); Serial.print(cmdA);
    Serial.print(  " cmdB:"); Serial.print(cmdB);
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

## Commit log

2024-11-11 Initial Project Commit
    [0603 Capacitor.FCStd, 0603 Resistor.FCStd, 1kg 80mm Load Cell HOLE DRILLING JIG.SLDPRT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]
2024-11-11 Added 3D model screenshots
    [ServoLoadCell.SLDASM]
